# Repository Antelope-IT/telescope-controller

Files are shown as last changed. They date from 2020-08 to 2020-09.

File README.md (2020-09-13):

# Telescope Drive Controller
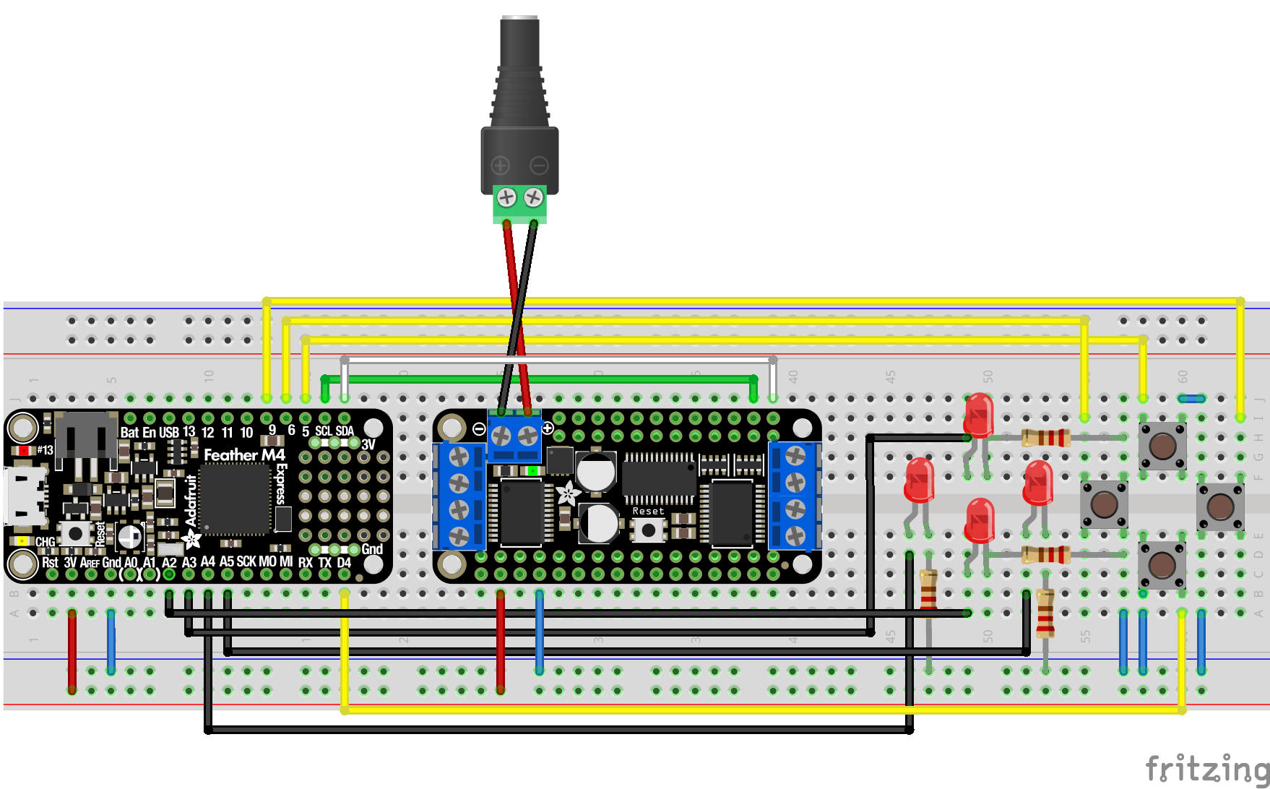
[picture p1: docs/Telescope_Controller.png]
Telescope controller Breadboard Layout


* [Overview](https://github.com/Antelope-IT/telescope-controller#Overview)
* [Hardware](https://github.com/Antelope-IT/telescope-controller#Hardware)
* [Software](https://github.com/Antelope-IT/telescope-controller#Software)
* [Calculations](https://github.com/Antelope-IT/telescope-controller#Calculations)
* [Future Work](https://github.com/Antelope-IT/telescope-controller#Future-Work)
* [Health Warning](https://github.com/Antelope-IT/telescope-controller#Health-Warning)

## Overview
This repository contains the source code and design schematics for a simple telescope drive controller for a telescope with basic stepper motor drives. The controller uses an [Adafruit M4 Feather Express](https://learn.adafruit.com/adafruit-feather-m4-express-atsamd51/overview) microcontroller
and the [Adafruit Stepper + DC Motor Feather wing](https://learn.adafruit.com/adafruit-stepper-dc-motor-featherwing) motor drive. The software is written in CircuitPython but could be adapted for different languages.

This project came about as a result of me inheriting a telescope with a German Equatorial Mount that was fitted with stepper motors for a motor drive but didn't have the controller box to power and control the stepper motors. 

The aim of this project was to see if it is possible to make the telescope mount work again and at the same time learn about microcontrollers and the Arduino ecosystem. 

## Hardware
The image above shows the breadboard layout, this layout is organic rather than logical. A more logical layout would be to put the microcontroller and motor drive board at either end of the breadboard leaving the space between for the control switches and indicators. This would result in shorter runs for the 8 control lines at the expense a slightly longer run for the I2C connection (shown green / white) which runs between the microcontroller and the motor drive board. Alternatively the motor drive and the microcontroller can be stacked which would remove the need for the long off board I2C connection at the expense of reduced accessibility for either the microcontoller board or the motor drive board (depending how they are stacked).

The direction of motion of the telescope is controlled via the four push to make switches. These are connected to microcontroller's digital inputs D4,D5,D6,D9. These have internal pull-up circuitry and so pull down to ground when pushed resulting a `False` when pushed. 

The four leds act as tell tales and indicate the direction of travel (its not obvious from the telescope due its speed of motion) these are connected to 4 digital outputs A2,A3,A4,A5 of the microcontroller. 

The leds are connected to ground via 220 Ohm resistors to limit the current flow and therefore the brightness of the leds. Increasing the size of these resistors will help reduce the power consumption of the board and the brightness of the leds thereby reducing light pollution in operation and help to preserve night vision.  

The stepper motors (not shown) are connected to the two connection blocks at either end of the motor drive board. The right ascension stepper motor is connected to stepper 1. The phases of the bipolar stepper motor is connected to the M1 and M2 terminals on motor drive board, respectively. Likewise, the declination stepper motor is connected to stepper 2 via the M3 and M4 terminals. 

Looking from the top of the motor drive board (as seen in the bread board image above), stepper 1 is at the left hand end of the motor drive board and stepper 2 is at the right hand end.   

A separate 6v 2A power supply provides the power for the stepper motors and is connected via the 2.1mm barrel connector.

A complete Fritzing breadboard and schematic layout can be found in the file controller.fzz in [docs](https://github.com/Antelope-IT/telescope-controller/tree/master/docs) directory (See Health Warning). 

### Components:
The parts lists is split into essential and optional components. Essential components represent the minimum required to make the solution work. 

The optional components listed allow the project to be more portable; disconnected from the main grid. With this in mind a suitably large usb battery pack with two outputs can be used to power the microcontroller and motor drive board simultaneously. A USB 5v to 6v buck converter is required to convert the 5v output from the battery pack to the 6v required to power the stepper motors.* 

In the case of the M4 Express Feather microcontroller a 3.7v LiPo battery can be connected to the microcontroller to power both the microcontroller and the motor drive board (logic only). This leaves the battery power pack free to power just the stepper motors.

All parts can be replaced with functionally compatible components and the code can be modified to suit.

#### Essential
* Microcontroller: [Adafruit M4 Feather Express](https://learn.adafruit.com/adafruit-feather-m4-express-atsamd51/overview)
* Motor Drive board: [Adafruit Stepper + DC Motor Feather wing](https://learn.adafruit.com/adafruit-stepper-dc-motor-featherwing)
* Motor Power Supply: 6v 1A+ Power supply with 2.1mm barrel connector (male)
* Microcontoller Power Supply: USB Power supply
* Connector for Motor Power: 2.1mm Barrel connector (female) - centre positive
* Stepper motor leads: 6p4c RJ11/RJ14 terminated
* Indicator LEDS: 4 x 3mm LED (red)
* 4 x 220 Ohm Resistors or higher for reduced light polution
* Control Switches: 4 x push to make switches

#### Optional
* USB Battery Pack 5V @ 3A 
* 3.7v LiPo battery
* Ripcord 5v -> 6v USB buck converter with 2.1mm barrel connector (male)

> *NB. This assumes that the buck converter is capable of supplying the power and sufficient current to drive the stepper motors. In my case I knew the original motor drive kit was designed to run from a 4 x D Cell battery pack providing a nominal 6v.
>
> The stepper motors are bipolar and by measurement the resistance for each phase was approximately 17-18 Ohms By Ohms law the current draw for each phase is expected to be 0.35A. If all 4 phases (2 x motors x 2 phases) are energised at the same time the current draw would be 1.4A.     
>
> The buck converter I'm using is rated at 9W => 1.5A and the battery power pack is rated at 3A so there should be sufficient headroom and room for error. In practice, in operation the current draw was measured at the output of the battery pack to be 0.9A with both steppers holding.
>
> The Adafruit Stepper + DC Motor Feather is capable of supplying 1.2A per coil/phase at voltages in the range 4.5v to 13.5v so 0.4A at 6v is well within the operating range of the device.

## Software
The code is written in CircuitPython version 5.3.0. The microcontroller will automatically load and run [code.py](https://github.com/Antelope-IT/telescope-controller/blob/master/src/code.py) at startup. The code has a setup phase followed by a continuous loop. The code has a number of dependencies (see below).

In the setup phase the hardware is initialised and timing constants are declared. The timing constants are used to divide the cycle rate of loop so that the stepper motors are advanced at the calculated intervals. Provided that the cycle rate of the loop is sufficiently faster than the rate of stepper motor movement this should be fine.

The defining timing constant is the raDelay constant - the calculation for which is shown below. This value is the delay in seconds between steps of the Right Ascension stepper motor needed to drive the telescope so that it tracks across the sky at the right speed (if the calculation is correct). The limitations of the stepper motors used means that it can't operate as a goto motor drive - the motors and gearing mean it can't physically move fast enough. To this end RA movement is essentially stop or go, future developments might be to add some means of finer adjustment. The DEC movement is simply for finer adjustment up and down this movement is four times the speed of the RA movement. The value four was selected because its known to give a rate of movement within the operating range of the stepper motors.

The motor step rates are further divided by 8 ( 4 x microsteps per single step / 32 ) to provide a clock rate to drive the indicator leds so that they flash when the motor is moving in indicated direction.

More work could be done to refine and improve this code but as there is no Decimal library for CircuitPython and no Async library (AFAIK) precision will be limited by the precision of the floating point library and the fastest rate at which the processor can traverse the loop of code. It also has to be remembered that not withstanding the limitations inherent in the code, there are also the limitations in the hardware; the stepper motors, gears etc.

### Libraries
The code has the folowing dependencies these are standard Adafruit libraries which can be found in the [CircuitPython libraries and drivers bundle](https://github.com/adafruit/Adafruit_CircuitPython_Bundle). Download the zip, extract it and copy the libraries to the CircuitPy/lib folder as required.

* Adafruit_Bus_Device
* Adafruit_Register
* Adafruit_PCA9685
* Adafruit SimpleIO
* Adafruit_Motor_Kit
* Adafruit_Motor

An additional dependency is the debouncer library this can be found in the [CircuitPython Community Bundle](https://github.com/adafruit/CircuitPython_Community_Bundle).

* Adafruit_Debouncer 

Add these libraries to the `\lib` folder in CircuitPy directory before running the code.

## Calculations

These calculations serve as a reminder as to how the figures in the code were arrived at, and for anyone wanting to replicate this project it should serve as a guide as to how to adapt the code to their own hardware (different stepper motors, different gearing).

```
  Stepper motor:
    steps / rotation (input shaft) = 48
    gear ratio input shaft : output shaft = 120:1
  
    Steps per rotation = 48 x 120 = 5760 steps per full rotation of the Stepper motor drive(output) shaft 
    
    The figures of 48 and 120 were found online but could be wrong - no identification markings on the stepper motors so no way to know for sure.
    The figure of 5760 has ben confirmed by experiment (to a good approximation).
    
  Telescope mount:
    By experiment 128 rotations of RA control to turn the telescope head through 360 degrees. (to a good approximation)
    
    Total steps required to turn the telescope head through 360 degrees = 128 x 5760 = _737280_
    
    1 day = 86400 sec 
    
    So to rotate the telescope head at the rate of 1 rotation per day the stepper motor needs to be driven at:
    
    737280 / 86400 steps/sec  = 8.5333 steps/sec
    
    This translates to 1 step every 1 / 8.5333s = 0.1171875s <= This gives the RA delay figure 
    
  Refinement:
    The sidereal day - the length of time before the stars are in the same place relative to the earth changes through the year but the mean sidereal day is
    23h 56m 4.0905s. If we take this figure as the length of the day then:
    
    737280 / 86164.0905 steps/sec  = 8.55669 s/s
  
    Which gives a delay of 0.1168675s between steps of the RA stepper motor and this is the figure in the code.
    
    NB. The length of a sidereal day, as given, is only an approximation. Comparing the results of using the two RA Delay figures, after running the mount for a whole day, the difference in pointing angle is just less than 1 degree.
```
## Future Work
### Software:
1. The code could be re-written using Arduino C This supports Asynchronous motor control and would allow for easier communication with a host computer via the USB connection allowing alternative modes of control.
2. Refinement of the code to improve performance and add features such as fine grained control of the telescope; RA adjustment as well as DEC adjustment. 
### Hardware:
1. Complete the hardware build by moving it to strip board or similar.
2. Encasing the components in a suitable enclosure to protect it from the elements.
3. Connections for the stepper motor drive leads seem fragile; replace with fly leads to off board female RJ11 6P4C connector and terminate both ends of the stepper motor drive leads with RJ11 connectors.
4. In general reduce light pollution from (leds), but add stepper motor power indicator and very dim led just to illuminate buttons. 

## Health Warning
The code and the schematics in this project work for me as I have built them; the mount moves as expected. The project as it is presented here is not a replacement for a consumer level motor drive; ~~its not very practical and~~ its not fully tested ~~- I am waiting to collect some missing parts for the mount before it can be fully assembled with a telescope to test it in the field.~~ and I have only done some initial testing but I can confirm that it does indeed work I was able to track Jupiter for an hour or so without problems. I suspect that at higher magnifications (4mm eyepiece) there is some detectable drift although this could just be me knocking the telescope while struggling to focus at the higher magnification. As noted above the stepper motor lead connections the seem fragile: the fine wires seem prone to break this could be resolved as noted above or by just applying some stress relief by way of added cable ties could work. Other than that the solution is more practical than I first thought, as it all just sits in the accessories tray of the mount. There are some images [here](https://github.com/Antelope-IT/telescope-controller/blob/master/docs) provided for illustration. 

The expected problems revolve around how effectively the controller can drive the stepper motors at the right speed and the power draw while its doing that. These are points for further experiment, refinement and devlopement. 

Under no circumstances use the contents of the Frizing document directly. It's a long time since I did anything like this and the first time I've done anything with that software and I really didn't have a clue what I was doing.  

The bread board view looks to be an accurate representation of what I have built, if you want to build this project or something based on it, then use the bread board view as a guide and check as you go that the links you are adding make sense. 

The schematics view looks to be technically correct but don't use it as an examplar of how to layout a circuit diagram. 

The pcb schematic should not be used under any circumstance. I have not used it to manufacture from and would recommend that you don't; it was purely a technical exercise to see if I could layout the board without crossing the beams. 

You are welcome to use what you see here and to learn from my mistakes but I make no guarantees regards the quality, functionality or suitability of this project for your application. You are free to use and adapt the information, ideas and designs contained in this project but you do so entirely at your own risk.

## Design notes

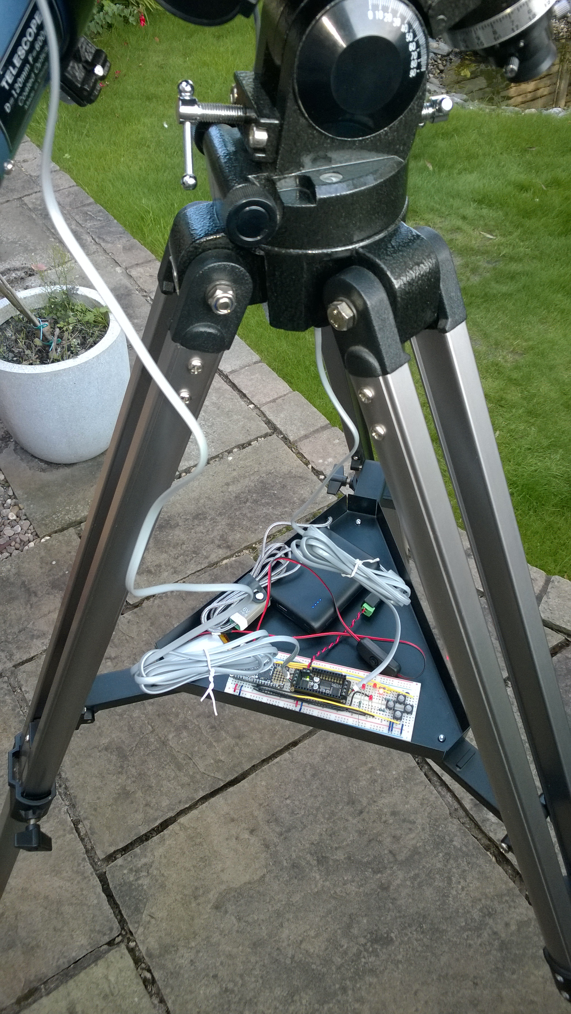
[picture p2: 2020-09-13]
docs/Telescope_Accessories_Tray.jpg

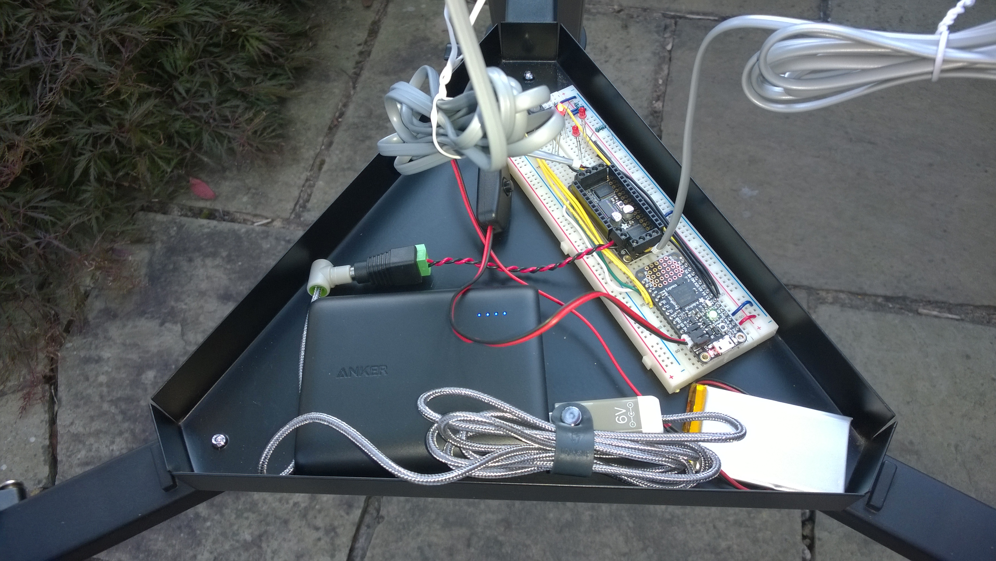
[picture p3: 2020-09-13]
docs/Controller_In_Accessories_Tray_1.jpg

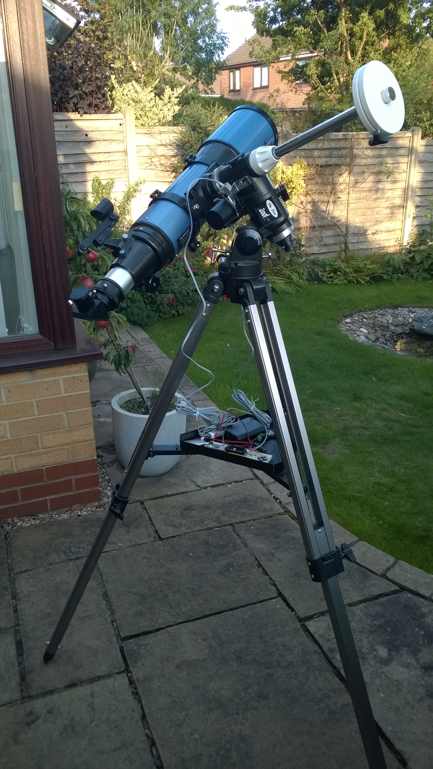
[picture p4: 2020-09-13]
docs/Telescope_On_Mount.jpg

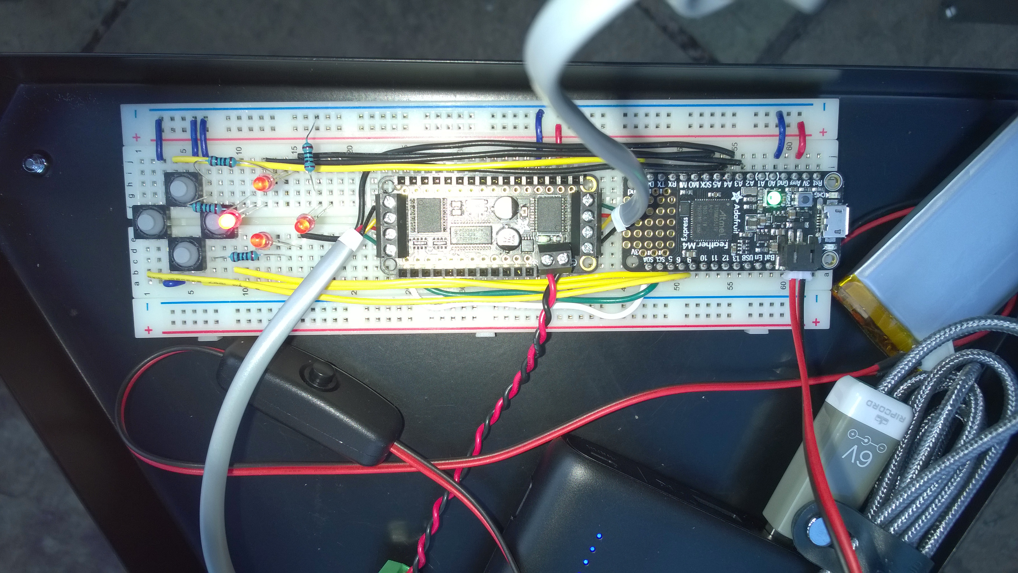
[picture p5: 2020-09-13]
docs/Controller_Board_Working.jpg

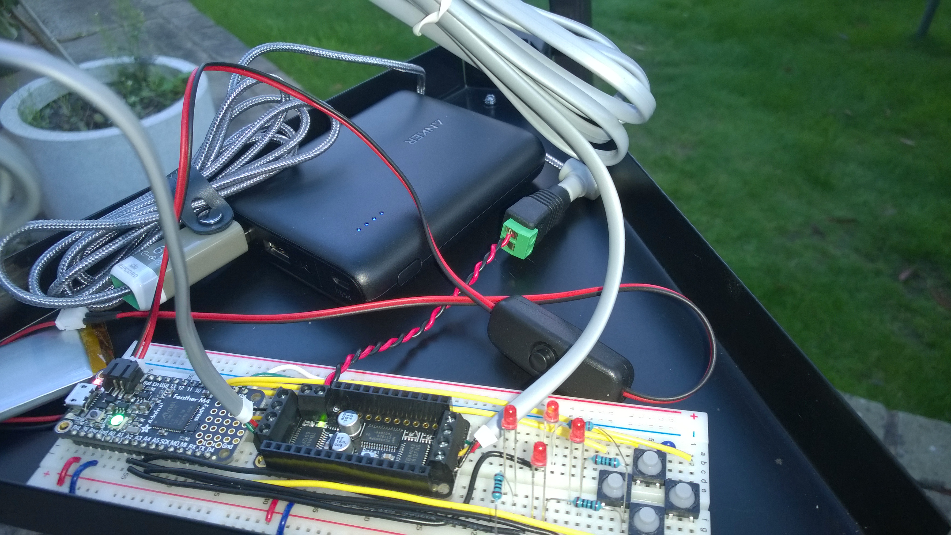
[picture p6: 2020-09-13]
docs/Controller_In_accessories_tray_2.jpg

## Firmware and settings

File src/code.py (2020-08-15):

from analogio import AnalogIn
from adafruit_motorkit import MotorKit
from adafruit_motor import stepper
from adafruit_debouncer import Debouncer

import board
import time
import simpleio
import digitalio

ledMain = simpleio.DigitalOut(board.D13)

vbat_voltage = AnalogIn(board.VOLTAGE_MONITOR)
kit = MotorKit(steppers_microsteps=4)

decDirection = stepper.BACKWARD
decStyle = stepper.SINGLE
decMove = False
decDelay = 0.116867
decMoving = False

raDirection = stepper.FORWARD
raStyle = stepper.SINGLE
raMove = False
raDelay = 0.116867
raMoving = False

def get_voltage(pin):
    return (pin.value * 3.3) / 65536 * 2

def make_output_led(pin):
    led = digitalio.DigitalInOut(pin)
    led.direction = digitalio.Direction.OUTPUT
    return led

def make_debouncable(pin):
    switch_io = digitalio.DigitalInOut(pin)
    switch_io.direction = digitalio.Direction.INPUT
    switch_io.pull = digitalio.Pull.UP
    return switch_io

ledDown = make_output_led(board.A2)
ledUp = make_output_led(board.A3)
ledLeft = make_output_led(board.A4)
ledRight = make_output_led(board.A5)

buttonDown = Debouncer(make_debouncable(board.D4))
buttonUp = Debouncer(make_debouncable(board.D5))
buttonLeft = Debouncer(make_debouncable(board.D6),0.5)
buttonRight = Debouncer(make_debouncable(board.D9),0.5)

kit.stepper1.release()
kit.stepper2.release()
raTriggerLatch = False

TICKS_PER_SEC = 1_000_000_000

heartbeatTicks = TICKS_PER_SEC
raLastTicks = 0
decLastTicks = 0
lastTicks = 0
lastUpDateTicks = 0

decRateTicks = (decDelay * TICKS_PER_SEC) // 4
raRateTicks = raDelay * TICKS_PER_SEC
UpdateTicks = 0.05  * TICKS_PER_SEC

while True:
    currentTicks = time.monotonic_ns();

    if currentTicks - UpdateTicks > lastUpDateTicks:
        lastUpDateTicks = currentTicks
        buttonDown.update()
        buttonUp.update()
        buttonLeft.update()
        buttonRight.update()

    raTrigger = (not buttonLeft.value or not buttonRight.value) and (not (buttonLeft.value and buttonRight.value))

    if raTrigger and not raTriggerLatch:
        raTriggerLatch = True
        raMove = not raMove
        if not buttonLeft.value:
            raDirection = stepper.BACKWARD
        elif not buttonRight.value:
            raDirection = stepper.FORWARD
    elif raTriggerLatch and not raTrigger:
        raTriggerLatch = False

    decMove = (not buttonUp.value or not buttonDown.value) and (not (buttonUp.value and buttonDown.value))

    if decMove:
        decDirection = stepper.FORWARD if buttonUp.value else stepper.BACKWARD

    if raMove:
        if (time.monotonic_ns() - raLastTicks > raRateTicks):
            raLastTicks = time.monotonic_ns()
            numsteps = kit.stepper1.onestep(direction=raDirection, style=raStyle)
            raMoving = True
            if numsteps % 32 == 0:
                if raDirection == stepper.FORWARD:
                    ledRight.value = not ledRight.value
                else:
                    ledLeft.value = not ledLeft.value

    else:
        if raMoving:
            kit.stepper1.release()
            ledRight.value = False
            ledLeft.value = False
            raMoving = False

    if decMove:
        if (time.monotonic_ns() - decLastTicks > decRateTicks):
            decLastTicks = time.monotonic_ns()
            numsteps = kit.stepper2.onestep(direction=decDirection, style=decStyle)
            decMoving = True
            if numsteps % 32 == 0:
                if decDirection == stepper.BACKWARD:
                    ledUp.value = not ledUp.value
                else:
                    ledDown.value = not ledDown.value

    else:
        if decMoving:
            kit.stepper2.release()
            ledUp.value = False
            ledDown.value = False
            decMoving = False

    currentTime = time.monotonic_ns()
    interval = currentTime - currentTicks

    if currentTicks - heartbeatTicks > lastTicks:
        ledMain.value = not ledMain.value
        lastTicks = currentTicks
        battery_voltage = get_voltage(vbat_voltage)
        print(f"Interval: {interval} VBat voltage: {battery_voltage:.2f}")
